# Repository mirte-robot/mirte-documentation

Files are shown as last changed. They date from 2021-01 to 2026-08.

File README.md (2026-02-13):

# Documentation MIRTE Robot

To build the documentation (requirement: Python3.10):

```sh
git clone https://github.com/mirte-robot/mirte-documentation
cd mirte-documentation
mkdir -p _modules/mirte-python
git clone https://github.com/mirte-robot/mirte-python _modules/mirte-python
python3 -m venv docs-env
source docs-env/bin/activate
pip install -r requirements.txt
cd _modules/mirte-python
pip install .
cd ../../

make html
# OR
sphinx-multiversion . _build/html
```

## Host locally
```
sphinx-reload . --watch doc/ _static/ _modules/  # browser will open automatically, don't forget the dot.
```
## Test

The documentation must pass the following two checks. Warnings are allowed, errors not.
```sh
make html && make linkcheck
```

## Spelling
Check for spelling with the following command
```sh
make spelling
```
Add correct words to the ```spelling_wordlist.txt``` file.

## Multi version setup
As the docs build uses other parts (ROS, Python, ...), just using sphinx-multiversion doesn't work 100%.
New setup:
- At release of a new version, a site.zip is created with the docs of that version without any other versions or version selector
- At creation of a new pages:
  - create dummy tags to generate the correct versions html
  - sphinx-multiversions build
  - for each release:
    - download the site.zip from the release page
    - take the versions html code from the 'dummy' and replace it in the downloaded version
  - push to github pages

How to create new version:
- change conf.py to new tag
- change _static/index.html to point to latest version.
- add new main version to build.yml:6: the releases env variable.

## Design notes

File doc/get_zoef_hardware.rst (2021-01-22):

Get the Zoef Hardware
#####################

Currently it is only possible to order all the parts yourself. In the futuer we will make it easier to buy a full Zoef Basic Box with all the listed components. 

Since we really want the robot to be upgradable, we will also support at least the mentioned alternatives/upgrades. At the moment the *italic* items are not yet supported though.

.. |check| raw:: html

    <input checked=""  type="checkbox">

+---------------------------+--------------------------------------------------+-------------------------------------------+
|                           | Zoef Basic                                       | Alternatives/Upgrades                     |
+===========================+==================================================+======================+====================+
| Computer                  | Orange Pi Zero (set 2 [1]_)                      | *Raspberry Pi 2/3/4* | *Jetson Nano 2GB*  |
+---------------------------+--------------------------------------------------+----------------------+--------------------+
| SD card                   | *TBD*                                            | Any 8Gb+ SD card                          |
+---------------------------+--------------------------------------------------+-----------------+-------------------------+
| Microcontroller           | STM32                                            | Arduino Nano    | *ESP8266*               |
+---------------------------+--------------------------------------------------+-----------------+-------------------------+
| Electrical circuit        | Zoef PCB                                         | Breadboard [3]_ | Powered breadboard [4]_ |
+---------------------------+--------------------------------------------------+-----------------+-------------------------+
| 3 pin cable               | 4x JST                                           | 4 x female-female dupont                  |
+---------------------------+--------------------------------------------------+-------------------------------------------+
| 4 pin cable               | 4x JST                                           | 4 x female-female dupont                  |
+---------------------------+--------------------------------------------------+-------------------------------------------+
| Micro USB cable 90 deg    |                                                  |                                           |
+---------------------------+--------------------------------------------------+ dupont cable                              |
| Micro USB cable short     |                                                  |                                           |
+---------------------------+--------------------------------------------------+-------------------------------------------+
| Battery                   | 5000mAh power bank [2]_                          | *12V battery pack with step down*         | 
+---------------------------+--------------------------------------------------+-------------------------------------------+
| Chassis                   | Zoef diff drive wood                             | *Zoef diff drive 3D print*                |
+---------------------------+--------------------------------------------------+-------------------------------------------+
| Nuts and bolts            | 15x M3                                           | *M3 with standoffs*                       |
+---------------------------+--------------------------------------------------+-------------------------------------------+
| Ball caster               | W420                                             |                                           |                 
+---------------------------+--------------------------------------------------+-------------------------------------------+
| Wheels                    | 2x Yellow TT motor wheel                         |                                           |
+---------------------------+--------------------------------------------------+-------------------------------------------+
| Motors                    | 2x TT motor male dupont                          | *TBD*                                     |
+---------------------------+--------------------------------------------------+-----------------+-------------------------+
| Motor driver              | L9110s                                           | L298N [5]_      | MX1919                  |
+---------------------------+--------------------------------------------------+-----------------+-------------------------+
| **Optional**                                                                                                             |
+---------------------------+--------------------------------------------------+-------------------------------------------+
| Wheel encoders            | 2x HC-020K                                       | *TBD*                                     |
+---------------------------+--------------------------------------------------+-------------------------------------------+
| Distance sensors          | 2x HC-SR04                                       |                                           |
+---------------------------+--------------------------------------------------+-------------------------------------------+
| Line follow sensors       | 2x TCRT5000                                      | *TBD*                                     |
+---------------------------+--------------------------------------------------+-------------------------------------------+
| Keypad                    | 5 button keypad                                  |                                           |
+---------------------------+--------------------------------------------------+-------------------------------------------+
| USB Camera                | HM1355                                           |                                           |
+---------------------------+--------------------------------------------------+-------------------------------------------+
| Displays                  | 2x 128x64 OLED                                   |                                           |
+---------------------------+--------------------------------------------------+-------------------------------------------+
| Servo                     | SG90                                             |                                           |
+---------------------------+--------------------------------------------------+-------------------------------------------+

.. [1] The extension board is optional, but needed when using the USB camera.
.. [2] This power bank will fit the wooden frame. Any powerbank with a stable 5V will work.
.. [3] With a breadboard, the JST and USB cables need to be replacd by dupont cables.
.. [4] With a powered breadboard the JST cables need to be replaced by dupont cables.
.. [5] Due to teh voltage drop this will not work well with a 5V powerbank.

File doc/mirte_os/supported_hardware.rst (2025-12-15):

.. _supported-hardware:

Supported Hardware
##################

Microcontroller Peripherals
***************************

Raw pins
========

.. tabs::

   .. group-tab:: ROS

      .. code-block:: bash

         $ ros2 service call /io/get_analog_pin_value mirte_msgs/srv/GetAnalogPinValue "{pin: }"
         $ ros2 service call /io/get_digital_pin_value mirte_msgs/srv/GetDigitalPinValue "{pin: }"
         $ ros2 service call /io/set_digital_pin_value mirte_msgs/srv/SetDigitalPinValue "{pin: ,value: false}"
         $ ros2 service call /io/set_pwm_pin_value mirte_msgs/srv/SetPWMPinValue "{pin: ,value: false}"

      Setting a pin can be either 'analog' (PWM) or 'digital'. The pin itself can be defined
      as the print on the MCU (e.g. 'GP3'). You can have a look in the web interface to
      see all options. 

   .. group-tab:: Python

      .. code-block:: python
      
         from mirte_robot import robot
         mirte = robot.createRobot()

         mirte.getAnalogPinValue()

      .. automethod:: robot.Robot.setAnalogPinValue
         :noindex:

      .. automethod:: robot.Robot.getAnalogPinValue
         :noindex:

      .. automethod:: robot.Robot.setDigitalPinValue
         :noindex:

      .. automethod:: robot.Robot.getDigitalPinValue
         :noindex:

   .. group-tab:: Blockly

      

.. warning::
    Currently there is no check on whether a pin is already in use by some hardware defined
    in the yaml configuration discussed earlier. Therefore there is no expected behavior 
    when using getting or setting raw pins.

DC Motor
========

Depending on the interface of your motor controller, the DC motor can be controlled though three
different interfaces:

   - **ddp** (digital, digital, pwm): This interface uses two digital pins to set the direction of
     the motor, and uses a PWM dignal to set the speed. The L298 can use this interface.
   - **dp** (digital, pwm): This interface uses one digital pin for teh direction, and pwm for the speed.
     The downside is that the motor will slightly 'kick' when switching between forward and backward.
     This can be done on both L298 and L9110.
   - **pp** (pwm, pwm): This interface uses two PWM signals to control the motor. The downside is that
     this will take up 2 PWM pins. Can be used on both L298 and L9110.

As you can see the choice for interface depends on the actual interface provided by the motor
controller, and the number of (PWM) pins you have available on the MCU.

ddp (e.g. L298)
---------------
.. code-block:: yaml

   motor:
     left:
       name: left
       device: mirte
       type: ddp
       pins:
         d1: GP19
         d2: GP18
         p1: GP17     # pwm

dp (e.g. L298 or L9110)
-----------------------

.. code-block:: yaml

   motor:
     left:
       name: left
       device: mirte
       type: dp
       pins:
         d1: GP19
         p1: GP18      # pwm

pp (e.g. L298 or L9110)
-----------------------

.. code-block:: yaml

   motor:
     left:
       name: left
       device: mirte
       type: pp
       pins:
         p1: GP19       # pwm
         p2: GP18       # pwm

.. tabs::

   .. group-tab:: ROS

      .. code-block:: bash

         $ ros2 service call /io/motor/left/set_speed mirte_msgs/srv/SetMotorSpeed "{speed: 50}"

   .. group-tab:: Python

      .. code-block:: python
      
         from mirte_robot import robot
         mirte = robot.createRobot()

         mirte.setMotorSpeed('left', 50)

      .. automethod:: robot.Robot.setMotorSpeed        
         :noindex:

   .. group-tab:: Blockly

      

The motors will be defined separately. In this case there are two motors called 'left_motor' and 
'right_motor', both controlled on the 'mirte' device defined above. The pins are set corresponding 
to the L9110s motor driver.

.. warning::
   
   Please not that it is adviced to call the motors 'left' and 'right'. You can chose your own names
   when you are only using these interfaces. In order to also get the ROS twist message (and steering
   in the web interface to work) you **need** to have the motors called 'left' and 'right'.

Servo
=====
.. code-block:: yaml

   servo:
     left:
       name: left
       device: mirte
       pins:
         pin: GP3

.. tabs::

   .. group-tab:: ROS

      .. code-block:: bash

         $ ros2 service call /io/servo/right/set_angle mirte_msgs/srv/SetServoAngle "{angle: 90, degrees: true}"

   .. group-tab:: Python

      .. code-block:: python
      
         from mirte_robot import robot
         mirte = robot.createRobot()

         mirte.setServoAngle('left', 90)

      .. automethod:: robot.Robot.setServoAngle        
         :noindex:

   .. group-tab:: Blockly

      

Keypad
======
.. code-block:: yaml

   encoder:
     left:
       name: left
       device: mirte
       pins:
         pin: GP28     # analog input

.. tabs::

   .. group-tab:: ROS

      As a topic (non-blocking):

      .. code-block:: bash

         $ ros2 topic echo /io/keypad/left

      As a service (blocking):

      .. code-block:: bash

         $ /io/keypad/left/get_key

   .. group-tab:: Python

      .. code-block:: python
      
         from mirte_robot import robot
         mirte = robot.createRobot()

         mirte.getKeypad('left')

      .. automethod:: robot.Robot.getKeypad        
         :noindex:

   .. group-tab:: Blockly

      

OLED
====
.. code-block:: yaml

   oled:
     left:
       name: left
       device: mirte
       pins:
         scl: GP5
         sda: GP4

.. tabs::
   
   .. group-tab:: ROS

      .. code-block:: bash

         $ ros2 service call /io/oled/right/set_text mirte_msgs/srv/SetOLEDText "{text: 'hello'}"

   .. group-tab:: Python

      .. code-block:: python
      
         from mirte_robot import robot
         mirte = robot.createRobot()

         mirte.setOLEDText('left', 'hello mirte')

      .. automethod:: robot.Robot.setOLEDText        
         :noindex:

   .. group-tab:: Blockly

      

Distance sensor
===============
.. code-block:: yaml

   distance:
     left:
       name: left
       device: mirte
       pins:
         trigger: GP7
         echo: GP6

.. tabs::
   
   .. group-tab:: ROS

      As a topic (non-blocking):

      .. code-block:: bash

         $ ros2 topic echo /io/distance/left/get_range

      As a service (blocking):

      .. code-block:: bash

         $ ros2 service call /io/distance/left/get_range mirte_msgs/srv/GetRange

   .. group-tab:: Python

      .. code-block:: python
      
         from mirte_robot import robot
         mirte = robot.createRobot()

         mirte.getDistance('left')

      .. automethod:: robot.Robot.getDistance
         :noindex:

   .. group-tab:: Blockly

      

IR sensor
=========
.. code-block:: yaml

   intensity:
     left:
       name: left
       device: mirte
       pins:
         digital: GP16
         analog: GP26     # analog input

.. tabs::
   
   .. group-tab:: ROS

      As a topic (non-blocking):

      .. code-block:: bash

         $ ros2 topic echo /io/intensity/left
         $ ros2 topic echo /io/intensity/left/digital

      As a service (blocking):

      .. code-block:: bash

         $ ros2 service call /io/intensity/left/get_analog mirte_msgs/srv/GetIntensity
         $ ros2 service call /io/intensity/left/get_digital mirte_msgs/srv/GetIntensityDigital

   .. group-tab:: Python

      .. code-block:: python
      
         from mirte_robot import robot
         mirte = robot.createRobot()

         mirte.getIntensity('left')

      .. automethod:: robot.Robot.getIntensity
         :noindex:

   .. group-tab:: Blockly

      

Color sensor
============
.. code-block:: yaml

   color:
     left:
       name: left
       device: mirte
       pins:
       pins:
         scl: GP5
         sda: GP4

.. tabs::

   .. group-tab:: ROS

      As a topic (non-blocking):

      .. code-block:: bash

         $ ros2 topic echo /io/color/left/hsl
         $ ros2 topic echo /io/color/left/rgb

      As a service (blocking):

      .. code-block:: bash

         $ ros2 service call /io/intensity/left/get_analog mirte_msgs/srv/GetIntensity
         $ ros2 service call /io/intensity/left/get_digital mirte_msgs/srv/GetIntensityDigital

   .. group-tab:: Python

      .. code-block:: python

         from mirte_robot import robot
         mirte = robot.createRobot()

         mirte.getColor('left')['h']

      .. automethod:: robot.Robot.getColor
         :noindex:

   .. group-tab:: Blockly

      

USB Camera
**********

By default the robot assumes you have connected the supported USB cam.
Currently only a ROS interface is defined.

.. tabs::

   .. group-tab:: ROS

      The camera image is published in three ways (using `ROS image transport <http://wiki.ros.org/image_transport>`_).

      .. code-block:: bash

         $ rostopic echo /webcam/image_raw
         $ rostopic echo /webcam/image_raw/compressed
         $ rostopic echo /webcam/image_raw/theora

Other USB Cameras
=================

In case you have another USB webcam, you might need to change the parameters of the `USB cam <https://wiki.ros.org/usb_cam>`_ to
reflect your webcam. This then needs to be changed in the `launchfile <https://github.com/mirte-robot/mirte-ros-packages/blob/3cbfac4a66425defc56f39b94bafca7794dd227e/mirte_bringup/launch/minimal.launch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>`_:

.. code-block:: bash      

   $ v4l2-ctl --list-formats-ext
   $ nano /home/mirte/mirte_ws/src/mirte_bringup/launch/minimal.launch

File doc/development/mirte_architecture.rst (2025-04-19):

Software Architecture Overview
##############################

.. warning::
   Currently none of the interfaces (hardware, software) are definitive. This means that we might still
   change this. Developing educational material around MIRTE is possible, but you should be able to
   modify this in case we change the interfaces.

Software Architecture
=====================

As the robot is meant for education, most of the design decisions we made were made with that in mind. This
means we were forced to make decisions in the speed vs usability (/learnability) tradeoff and decided to go
for the learnability over speed. We this improving speed should, at some point, be done by the students
themselves.

.. tabs::

   .. tab:: Overall

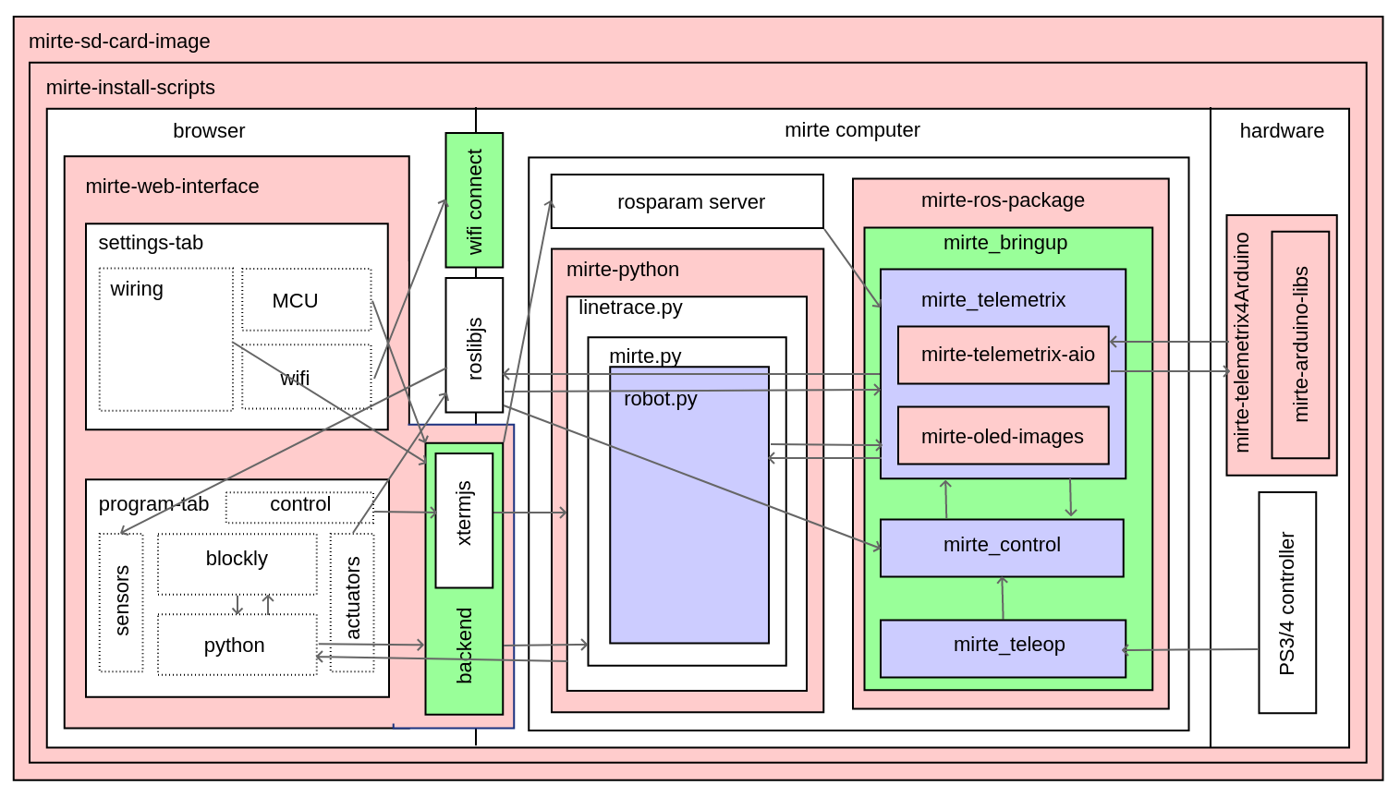
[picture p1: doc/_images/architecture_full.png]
Full Software Architecture
      

      Full architecture overview of the MIRTE software. Repositories are shown in red, ROS nodes in blue, and
      systemd services in green. More explanation can be found in the corresponding tabs. The dataflow is
      shown with arrows and will be explained in the next section.

   .. tab:: Repositories

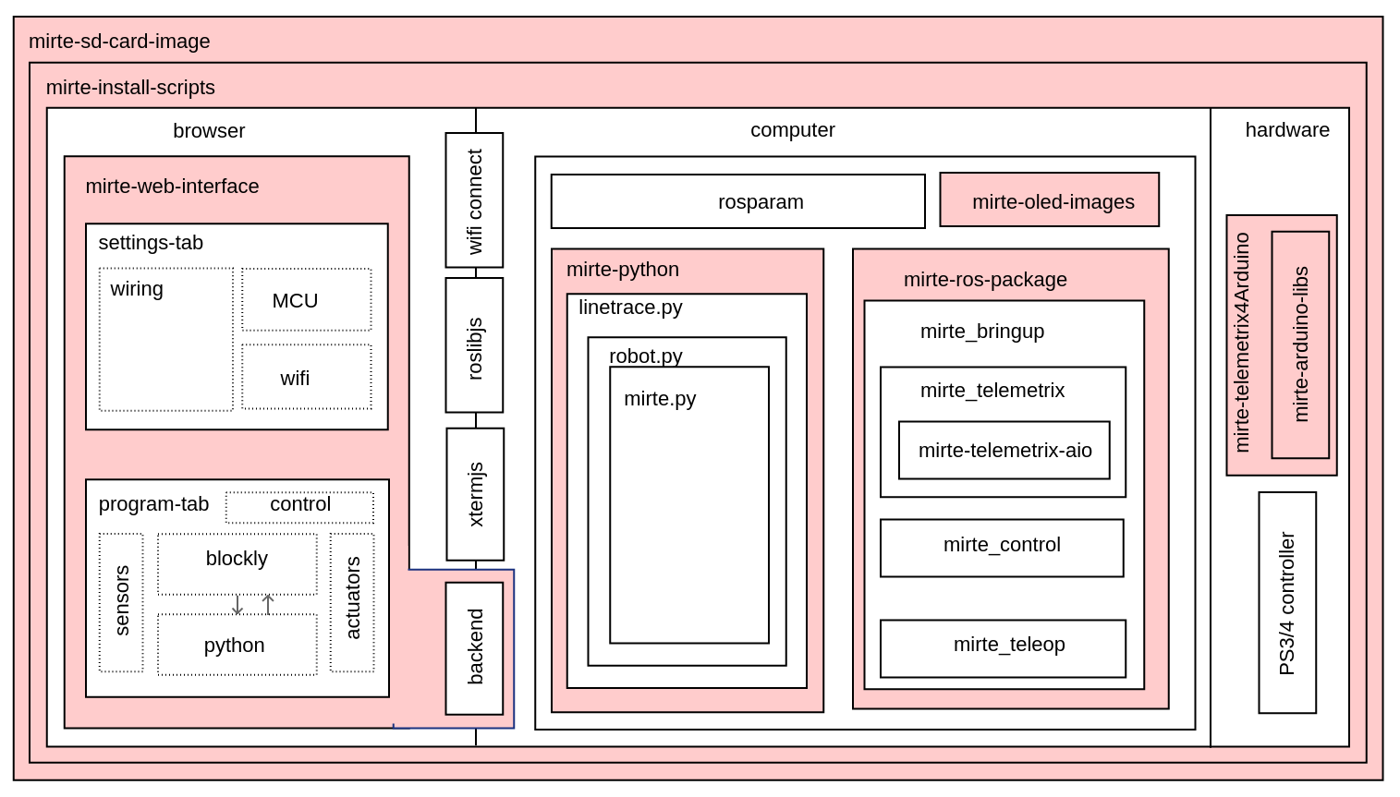
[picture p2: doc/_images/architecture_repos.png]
Overview of software repositories.
      

      The software of MIRTE is stored in multiple repositories on `github <https://github.com/mirte-robot>`_, 
      but can also be found on the MIRTE robot in /usr/local/src/mirte. 
 
      - `mirte-web-interface <https://github.com/mirte-robot/mirte-web-interface>`_: Is the repository 
        where the Vue frontend and nodeJS backend are stored. They are in one repository since they are 
        frequently updated together.
      - `mirte-python <https://github.com/mirte-robot/mirte-python>`_: Contains the python API of the
        sensors and actuators. This basically is a wrapper around the ROS topics and services for all
        the sensors and actuators.
      - `mirte-ros-packages <https://github.com/mirte-robot/mirte-ros-packages>`_: Contains the ROS packages
        to communicate with the hardware (MCU, PS controller, camera, etc) and the differential drive controller.
      - `mirte-telemetrix-aio <https://github.com/mirte-robot/telemetrix-aio>`_: Is a fork of
        telemetrix-aio to also support our own wheel encoder library (needed to get the interrupts of the encoder).
      - `mirte-telemetrix4Arduino <https://github.com/mirte-robot/Telemetrix4Arduino>`_: Is a fork 
        of telemetrix4Arduino to also add support for the wheel encoder.
      - `mirte-arduino-libraries <https://github.com/mirte-robot/mirte-arduino-libraries>`_: Contains the
        implementation of our own wheel encoder.
      - `mirte-oled-images <https://github.com/mirte-robot/mirte-oled-images>`_: Contains the images and
        image sequences to show on the OLED.
      - `mirte-install-scripts <https://github.com/mirte-robot/mirte-install-scripts>`_: Contains all scripts
        needed to install the MIRTE software on the robot. This includes our own repositories and dependencies,
        but also creates a user and enables the Wifi AP and systemd services.
      - `mirte-sd-image-tools <https://github.com/mirte-robot/mirte-sd-image-tools>`_: Contains all things 
        needed to build an ARM sd card image with everything installed from the mirte-install-scripts repo 
        for both the Orange Pi Zero 2 (Armbian Ubuntu) and Raspberry Pi (Ubuntu). 

   .. tab:: ROS nodes

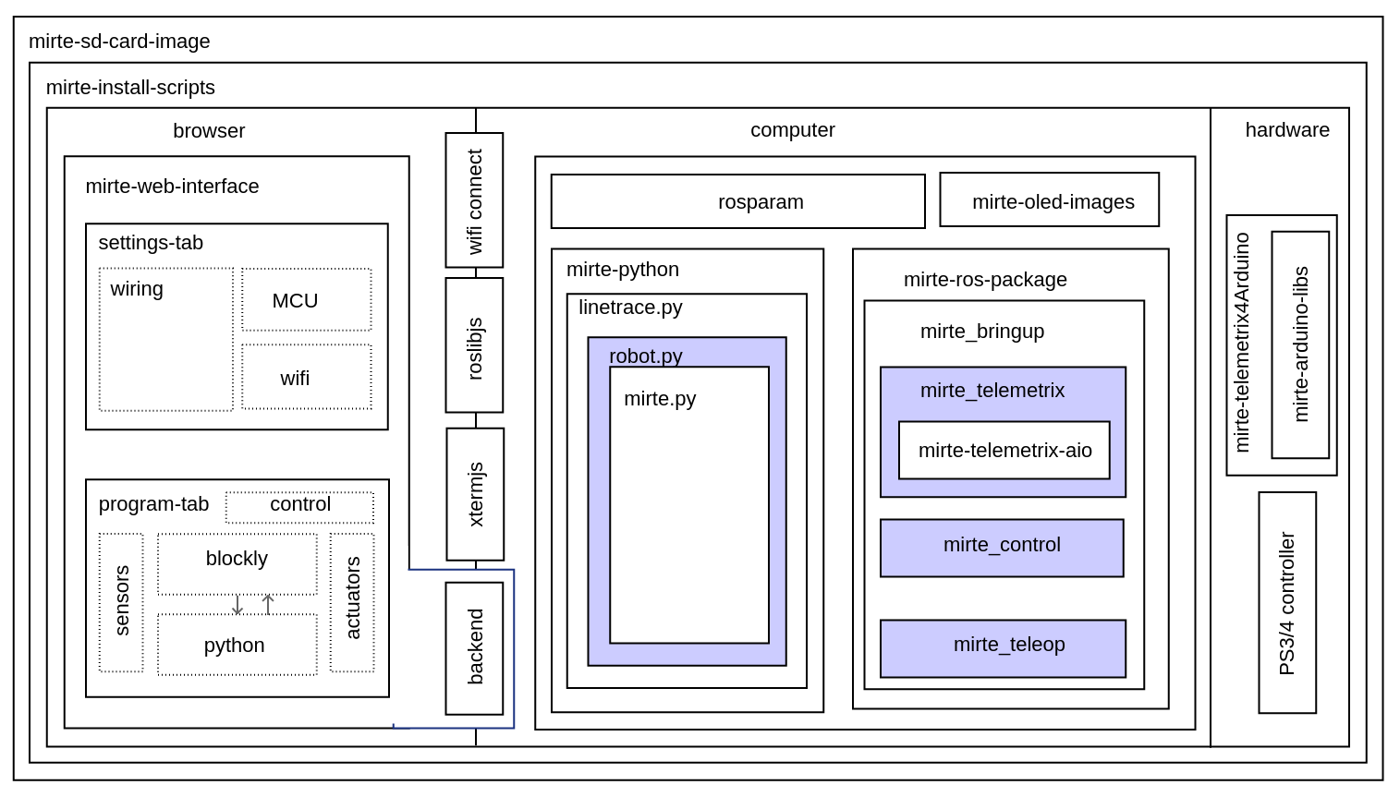
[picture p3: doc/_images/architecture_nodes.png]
Overview of ROS nodes.
      

      A couple of ROS nodes are used to control the robot (please note that the default for ROS packages
      are underscores):

      - **mirte_telemetrix**: This node initializes the telemetrix-aio pins based on the settings in the ROS
        parameter server. Each actuator will create a corresponding service. Each sensor will create
        both a service and a topic.
      - **mirte_control**: This is the ROS control wrapper for a differential drive robot. ROS control
        will already account for the kinematics from Twist message to rad/s per wheel. This rad/s per
        wheel is then transformed to speed (range -100 to 100) of the robot. 
      - **mirte_teleop**: This can be the teleop-key or teleop-joy node. In both cases the input from the
        device will be transformed into a Twist message.
      - **robot.py**: The robot.py node is included in the user defined python script. When run, this will
        start as a node as well. This node is only active when the user runs their script.

   .. tab:: Systemd

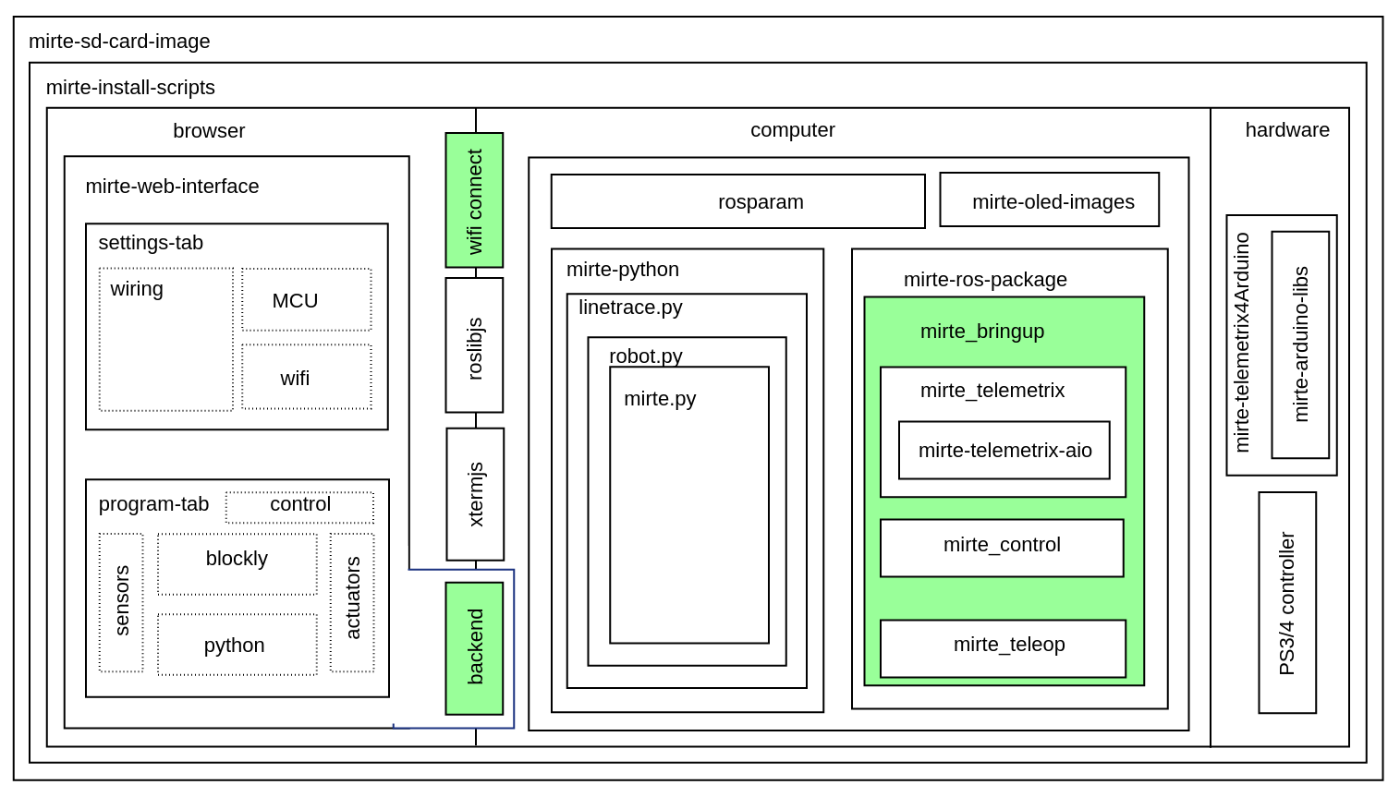
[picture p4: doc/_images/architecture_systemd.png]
Systemd services.
      

      In order to start all needed software on boot there are 3 systemd services activated:

      - **mirte-ap**: Service which starts the wifi-connect software. This will bring up a Wifi AP when
        no connection to a known network can be established. Otherwise it will connect to the known
        router. This service is executed as root.
      - **mirte-web-interface**: Service starts the web interface backend. The backend will also serve
        the frontend built by VueJS. This service is executed as the mirte user.
      - **mirte-ros**: Service will bringup ROS by launching minimal.launch.  This service is executed 
        as the mirte user.
      - **mirte-jupyter**: Service will start Jupyter Notebook which can be accessed on port 8888.

      All of them will start at boot, but can also be stopped:

      .. code-block:: bash

         mirte$ sudo service mirte-ros stop

      , started:

      .. code-block:: bash

         mirte$ sudo service mirte-ros start

      , or inspected:

      .. code-block:: bash

         mirte$ sudo journalctl -u mirte-ros -f

Software Flows
==============

.. tabs::

   .. tab:: Settings

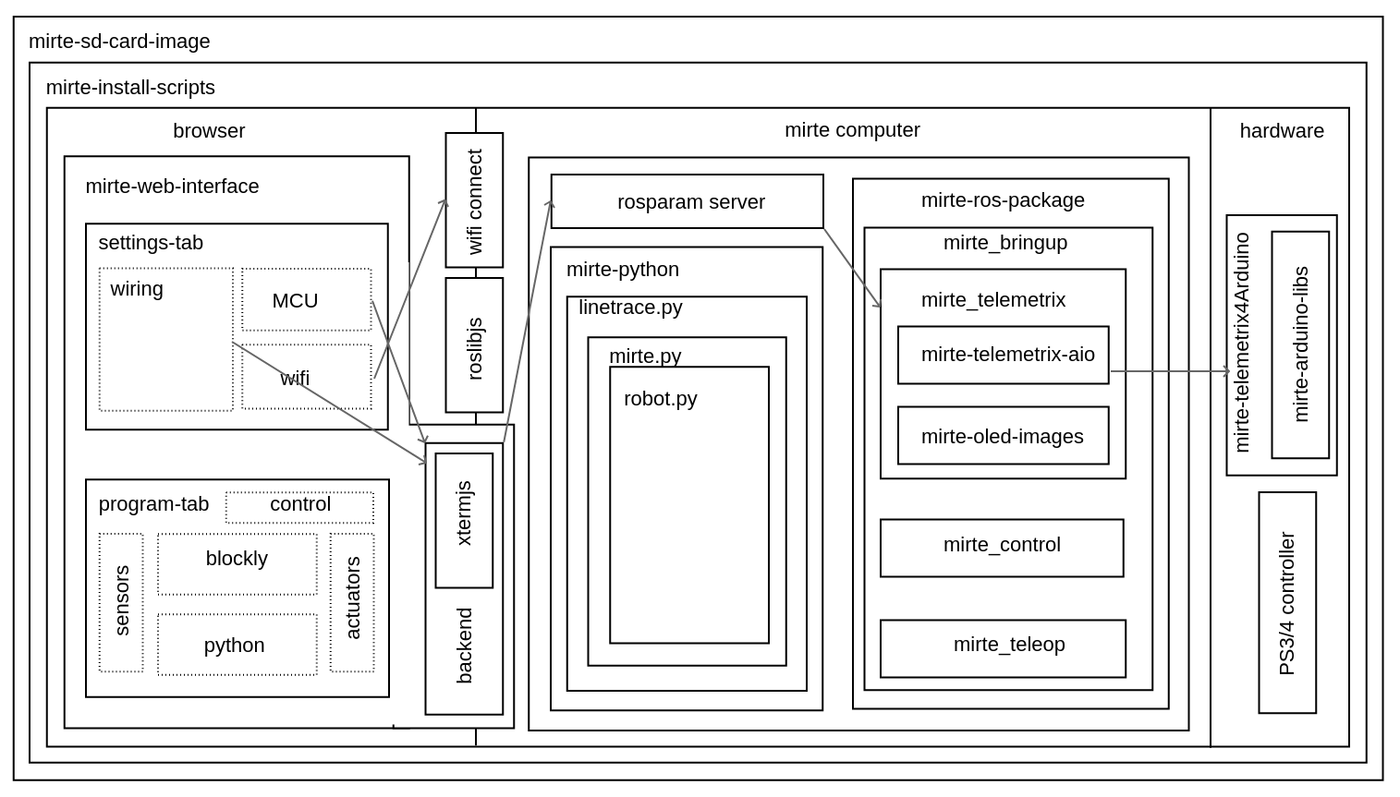
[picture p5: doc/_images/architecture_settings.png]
Settings flow.
      

      Like described earlier there are some things that you need to set before you can use the
      robot. This involves both uploading telemetrix to the MCU, and defining the connected
      hardware. Both can be done via commandline and web interface.

      When uploading telemetrix to the MCU from the web interface, a request will be sent to 
      the backend to execute the same command as you would execute when in a terminal.

      When a user changes the settings in the web interface a YAML file is generated and uploaded 
      via the backend to the robot. This will overwrite the mirte_user_config.yaml file and 
      overwrite the parameters in the running parameter server. The backend will also stop the 
      running telemetrix node and restart it so the initialization will be done again with the new 
      parameters. By restarting the telemetrix node, this node will get the new settings from
      the parameter server and initialize this using mirte-telemetrix-aio which will apply it
      on the MCU with mirte-telemetrix4Arduino.

      You can also connect to your own wifi. Whe doing this from the web interface, it will
      communicate the change right away to the wifi-connect server which will use NetworkManager
      accordingly.

      .. note::

         In the current implementation the YAML config is generated in the web interface
         and uploaded to the robot through the backend. We will redesign this in the future
         and implement a version where the web interface will communicate via roslibjs and
         therefore also be able to reflect the settings as they are.

      .. note::

         Usually one does not change the parameters within a running ROS system. We do think
         that these kind of settings belong to the parameter server since they usually do not
         change. In this educational robot we try to also make it easy to modify your robot.

   .. tab:: Sensors

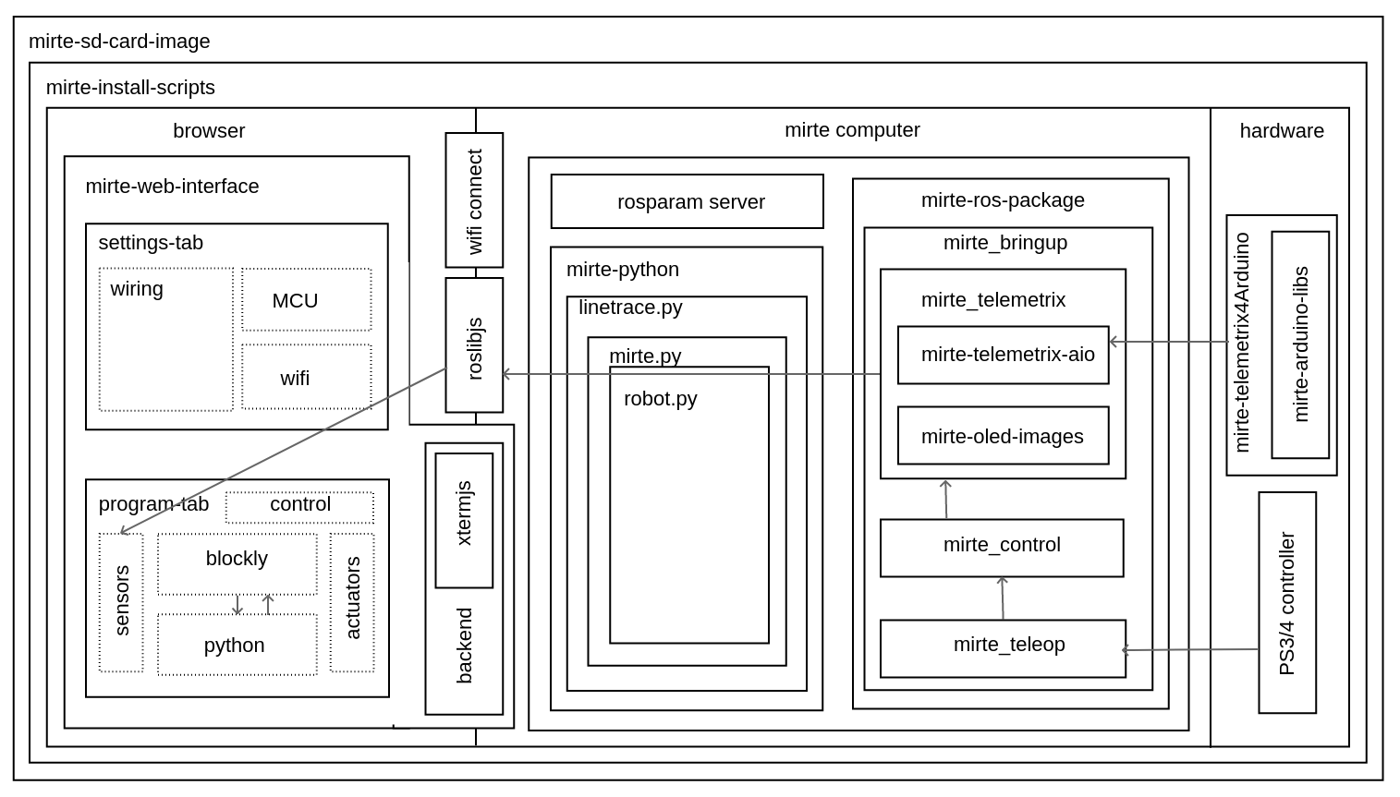
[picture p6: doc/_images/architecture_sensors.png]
Sensor data flow.
      

      Sensordata are read continuously in telemetrix (with a preset frequency). They are then
      communicated over USB from the MCU via mirte-telemetrix4Arduino to mirte-telemetrix-aio.
      The ROS node ROS_telemetrix_api.py from mirte_telemetrix will read these values as they
      get in via the callback from mirte-telemetrix-aio. They will then be published as a topic,
      and the last value is stored in order to be returned by a service call. These sensor
      values will the be send to the webinterface via roslibjs.

   .. tab:: Actuators

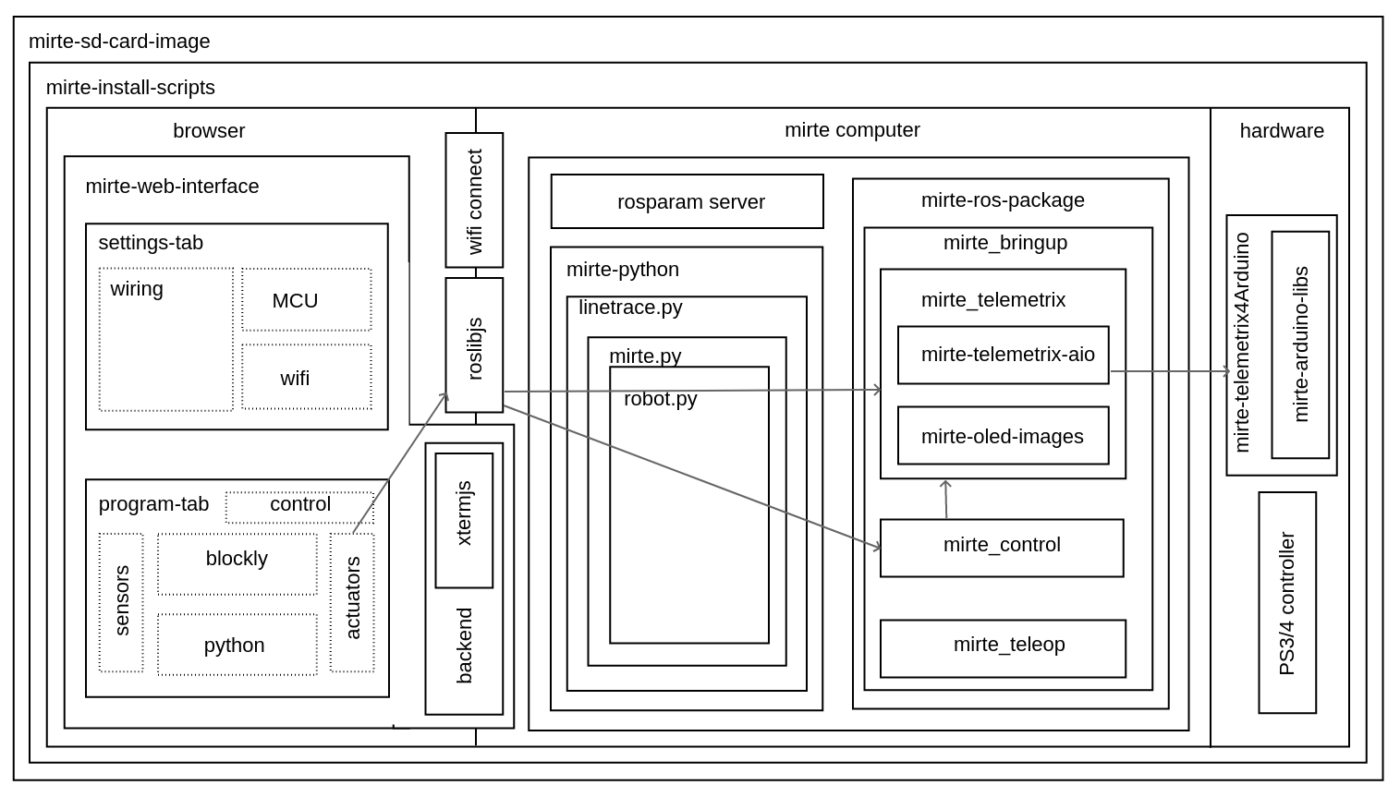
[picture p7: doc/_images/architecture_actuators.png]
Actuator data flow.
      

      When a user changes the actuator values in the web interface this will be communicated to
      the ROS_telemetrix_api.py node from mirte-telemetrix-aio (or to mirte-control in case 
      a Twist message is generated to drive around). The ROS_telemetrix_api.py node will the
      call the corresponding mirte-telemetrix-aio function which will pass this to 
      mirte-telemetrix4Arduino on the MCU.

   .. tab:: Python

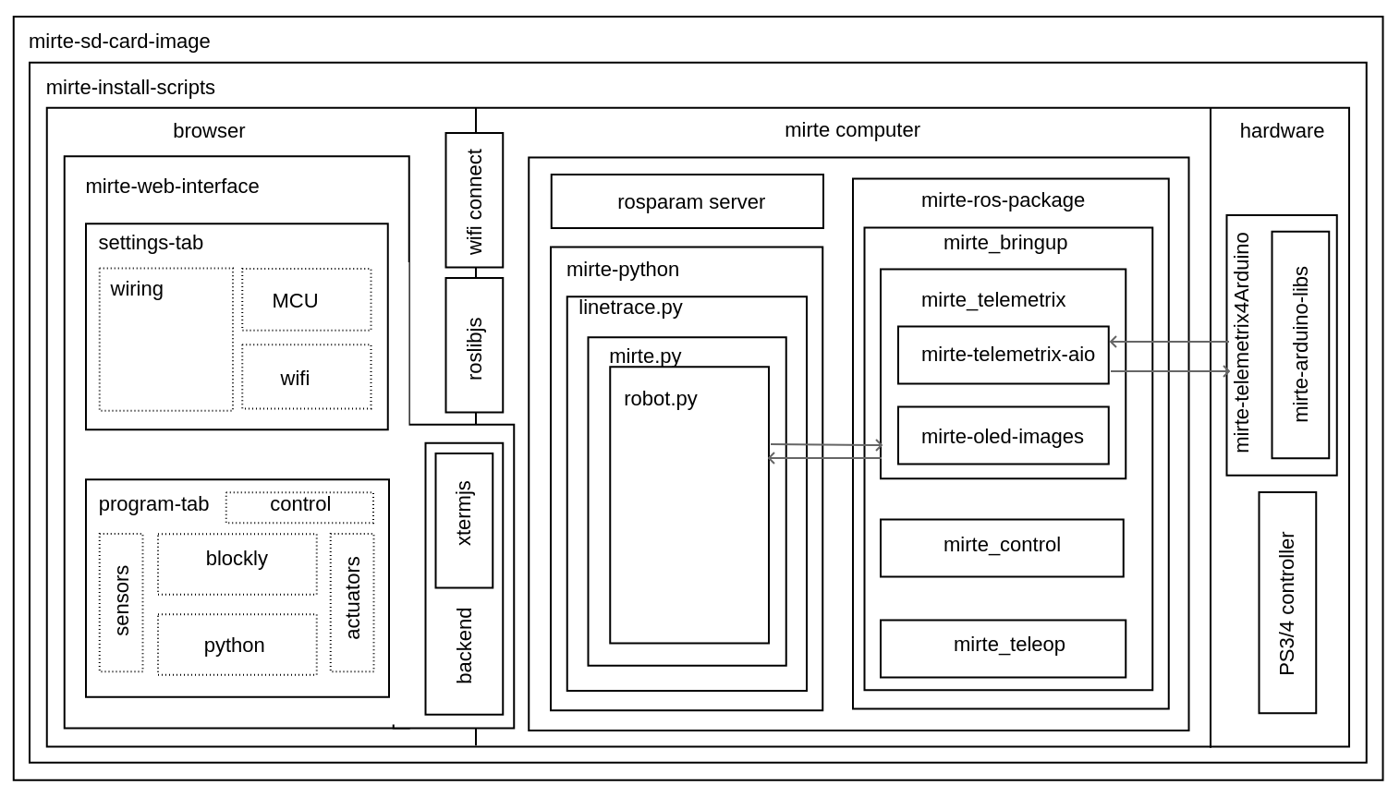
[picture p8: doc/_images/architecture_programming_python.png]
Python programming flow.
      

      TODO

   .. tab:: Blockly

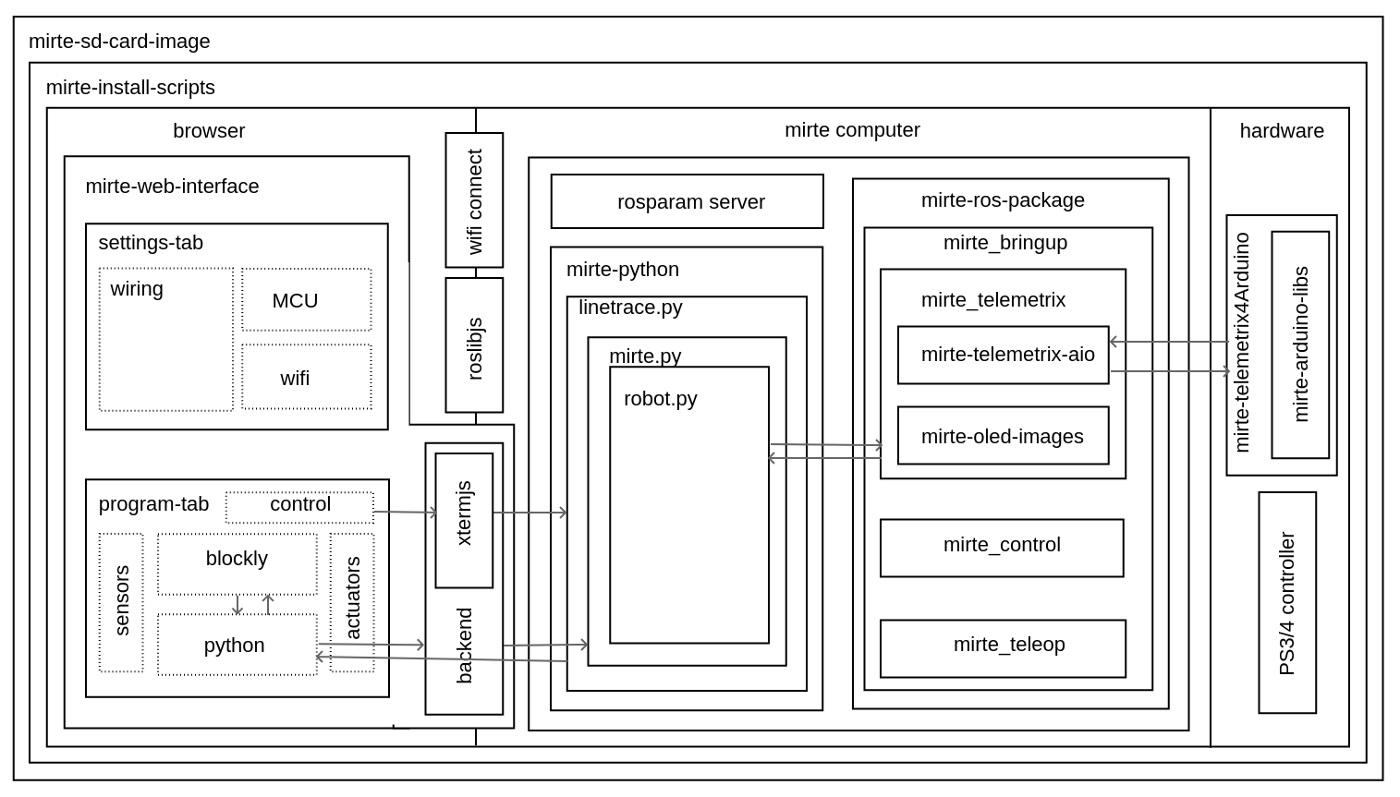
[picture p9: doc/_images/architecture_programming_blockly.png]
Blockly programming flow.
      

      TODO

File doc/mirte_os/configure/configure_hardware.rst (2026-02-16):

Specify Hardware
================

This step in only needed in case you are not using the MIRTE PCB (or followed the 
breadboard instructions). For other MCUs (or other wiring of the Raspberry Pi Pico) the software still
needs to know which pin is connected to what kind of hardware. This can be done in two ways.

From the Web Interface
----------------------

On the webinterface this can be done by removing and adding the peripherals in order
to match your robot hardware:

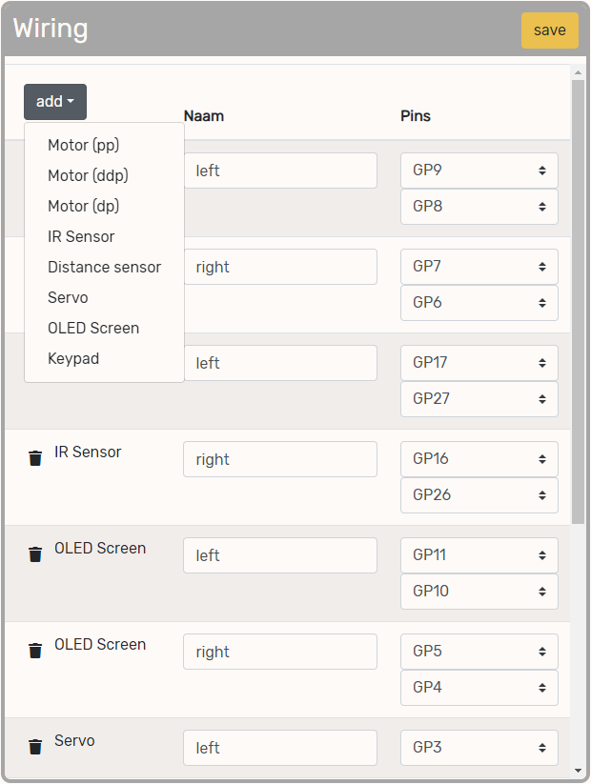
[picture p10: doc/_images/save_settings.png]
Save settings
      

From the Terminal
-----------------

The configuration to map the pins to sensortypes is done in `/usr/local/src/mirte/mirte-ros-packages/mirte_bringup/telemetrix_config/mirte_user_config.yaml <https://github.com/mirte-robot/mirte-ros-packages/blob/main/mirte_bringup/telemetrix_config/mirte_user_config.yaml>`_. 
This file consists of multiple sections needed for MIRTE to know which pins to control. 
The default settings are the MIRTE PCB. Below we will got though all sections (of the 
Raspberry Pi Pico on a breadboard).

.. code-block:: yaml

   device:
     mirte:
       type: breadboard
       board: pico                     # [pico, blackpill_f103c8, nanoatmega328]
       max_frequency: 50

Each config needs to state which type of device is is controlling. In this case we have 
one device called 'mirte' of type 'breadboard' with a 'pico' on it. The sampling frequency
is set to 50Hz, so every 2ms new sensor data will come in. Please note that your 
max_frequency might depend on the number of sensors you have connected. The more sensors
you connect, the lower the sampling frequency can get. If your sampling frequency is too
high you will notice a delay in the data.

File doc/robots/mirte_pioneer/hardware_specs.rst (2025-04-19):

Hardware specs
##############

One of the goals of MIRTE is to be modular and extendable. Therefore MIRTE has a minimal amount
of custom designed components, and mostly uses frequently used hardware. Two exceptions are
the `base <https://github.com/mirte-robot/mirte-frame>`_ (which can be lasercut, 3D printed, or 
any existing base you already have) and the `PCB <https://github.com/mirte-robot/mirte-pcb>`_ 
(which is optional and can be replaced by a breadboard as well). 

Below you will find the components that are used in the MIRTE Pioneer kit, which gives you a basic
mobile platform, and can be extended with optional sensors and actuators. Or you could use
alternatives/upgrades for certain parts.

Currently it is only possible to order all the parts yourself. In the future we will make it easier
to buy a full MIRTE Pioneer Box with all the listed components.

.. list-table::
   :widths: 25 25 50
   :header-rows: 1

   * - 
     - MIRTE Pioneer
     - Alternatives/Upgrades
   * - Computer
     - `Orange Pi Zero 2 <http://www.orangepi.org/html/hardWare/computerAndMicrocontrollers/details/Orange-Pi-Zero-2.html>`_
     - Raspberry Pi 3/4, Orange Pi 3B
   * - micro SD card
     - Intenso 16Gb (class 10) micro SD card
     - Any 16Gb+ micro SD card 
   * - Microcontroller
     - Raspberry Pi Pico H (RP2040)
     - Arduino Nano/Uno | SMT32 
   * - Electrical circuit
     - `MIRTE PCB <https://github.com/mirte-robot/mirte-pcb>`_
     - Breadboard [#f1]_ + `MB102 <https://www.aliexpress.com/item/1005001863057390.html>`_ + `splitter <https://www.aliexpress.com/item/4001025724405.html>`_
   * - 3 pin cable
     - 4x JST XH
     - 4x female-female dupont
   * - 4 pin cable
     - 4x JST XH
     - 4x female-female dupont
   * - Micro USB cable short
     - 1x
     - Dupont Cables
   * - Battery
     - `Intenso XS10000 <https://www.intenso.de/en/products/powerbanks/xs5000-xs10000-xs20000>`_
     - Any stable powerbank [#f2]_
   * - Chassis
     - `MIRTE diff drive wood <https://github.com/mirte-robot/mirte-frame>`_
     - MIRTE diff drive 3D print
   * - Nuts and bolts
     - 15x M3 15mm
     -
   * - Ball caster
     - `W420 (thin shape) <https://www.aliexpress.com/item/32734869856.html>`_
     -
   * - Wheels
     - `2x Yellow TT motor wheel <https://www.aliexpress.com/item/4000122298687.html>`_
     -
   * - Motors
     - `2x TT motor male dupont <https://www.aliexpress.com/item/32918824820.html>`_
     -
   * - Motor driver
     - `L9110s <https://www.aliexpress.com/item/32679413836.html>`_
     - `L298N <https://www.aliexpress.com/1005001621936295.html>`_ [#f3]_,  `MX1919 <https://www.aliexpress.com/item/32954393390.html>`_
   * - **Optional**
     -
     -
   * - Distance sensors
     - `2x HC-SR04 <https://www.aliexpress.com/item/4000232170787.html>`_
     -
   * - Line follow sensors
     - `2x TCRT5000 <https://www.aliexpress.com/item/32968870340.html>`_
     -
   * - Keypad
     - `5 button keypad <https://www.aliexpress.com/item/2044851328.html>`_
     -
   * - Displays
     - `2x 128x64 I2C OLED <https://www.aliexpress.com/item/1005001621806398.html>`_
     -
   * - Servo
     - `SG90 <https://www.aliexpress.com/item/1005001621918352.html>`_
     - Any servo supported by Arduino
   * - USB Camera
     - `OV9726 <https://www.aliexpress.com/item/1005005093538299.html>`_
     - Any USB camera

.. rubric:: Footnotes

.. [#f1] With a breadboard, the JST and USB cables need to be replaced by dupont cables.
.. [#f2] This power bank will fit the wooden frame. Any powerbank with a stable 5V will work.
.. [#f3] Due to the voltage drop of the L298N this will not work nicely with a 5V powerbank.

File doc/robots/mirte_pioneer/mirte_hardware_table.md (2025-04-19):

:orphan:

| | MIRTE Pioneer | Alternatives/Upgrades |
| --- | --- | --- |
| Computer | [Orange Pi Zero 2](http://www.orangepi.org/html/hardWare/computerAndMicrocontrollers/details/Orange-Pi-Zero-2.html) | | 
| SD card | Intenso 8Gb | Any 8Gb+ SD card | 
| Microcontroller | Raspberry Pi Pico (RP2040) | Arduino Nano/Uno or SMT32
| Electrical | [MIRTE PCB](https://github.com/mirte-robot/mirte-pcb) | Breadboard [^1] + circuit [MB102](https://www.aliexpress.com/item/1005001863057390.html) + [splitter](https://www.aliexpress.com/item/4001025724405.html) | 
| 3 pin cable | 4x JST XH | 4 x female-female dupont | 
| 4 pin cable | 4x JST XH | 4 x female-female dupont | 
| Micro USB cable short | 1x | Dupont Cables | 
 | Battery | [Intenso XS10000](https://www.intenso.de/en/products/powerbanks/xs5000-xs10000-xs20000/) | Any stable powerbank [^2] | 
 | Chassis | [MIRTE diff drive wood](https://github.com/mirte-robot/mirte-frame) | MIRTE diff drive 3D print | 
 | Nuts and bolts | 15x M3 | | 
 | Ball caster | [W420 (thin shape)](https://www.aliexpress.com/item/32734869856.html) | | 
 | Wheels | [2x Yellow TT motor wheel](https://www.aliexpress.com/item/4000122298687.html) | | 
 | Motors | [2x TT motor male dupont](https://www.aliexpress.com/item/32918824820.html) | | 
 | Motor driver | [L9110s](https://www.aliexpress.com/item/32679413836.html) | [L298N](https://www.aliexpress.com/item/1005001621936295.html) [^3] or [MX1919](https://www.aliexpress.com/item/32954393390.html) | 
 | **Optional** | | 
 | Distance sensors | [2x HC-SR04](https://www.aliexpress.com/item/4000232170787.html) | | 
 | Line follow sensors | [2x TCRT5000](https://www.aliexpress.com/item/32968870340.html) | | 
 | Keypad | [5 button keypad](https://www.aliexpress.com/item/2044851328.html) | | 
 | Displays | [2x 128x64 I2C OLED](https://www.aliexpress.com/item/1005001621806398.html) | | 
 | Servo | [SG90](https://www.aliexpress.com/item/1005001621918352.html) | Any servo supported by Arduino | 
 | USB Camera | [OV9726](https://www.aliexpress.com/item/1005005093538299.html) | Any USB camera | 
----------------------

**Footnotes**

[^1]: With a breadboard, the JST and USB cables need to be replaced by dupont cables.

[^2]: This power bank will fit the wooden frame. Any powerbank with a stable 5V will work.

[^3]: Due to the voltage drop of the L298N this will not work nicely with a 5V powerbank.

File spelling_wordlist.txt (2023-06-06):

Mirte
mirte
Arduino
arduino
Linux
linux
Blockly
blockly
mDNS
bluetooth
bluetoothctl
passwd
Telemetrix
telemetrix
Nano
Uno
launchfile
platformio
wifi
ini
systemd
bringup
api
cpp
scp
Jupyter
ROS
microcontroller
IP
hostname
Teleop
cmd
vel
PWM

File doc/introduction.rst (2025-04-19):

MIRTE (MIRTE, an Inspiring Robot for Technology Education) is yet another robot developed for
education. Robotics, due to the its multidisciplinary nature, is a good way to teach about STEM
eduction. This is why a lot of robotics kits have been developed already. So why yet another?
We believe that robotic kits for education should be cheap, open source, not only focus on the
software, have as few custom parts as possible, and should be useful from primary/elementary school
all the way to university. Getting you to the next level in each discipline step by step.

+-------------+--------------------------------------------------------------------------------------------------------------------------------+
| Software    | from `Blockly <https://developers.google.com/blockly>`_ to `Python <https://www.python.org/>`_ to `ROS <https://www.ros.org>`_ |
+-------------+--------------------------------------------------------------------------------------------------------------------------------+
| Electrical  | from custom PCB with Raspberry Pi Pico (RP2040), to breadboard with STM32/Arduino                                              |
+-------------+--------------------------------------------------------------------------------------------------------------------------------+
| Mechanical  | from wooden frame to own made (3D printed) frames                                                                              |
+-------------+--------------------------------------------------------------------------------------------------------------------------------+
| Interaction | from cute to purely functional                                                                                                 |
+-------------+--------------------------------------------------------------------------------------------------------------------------------+

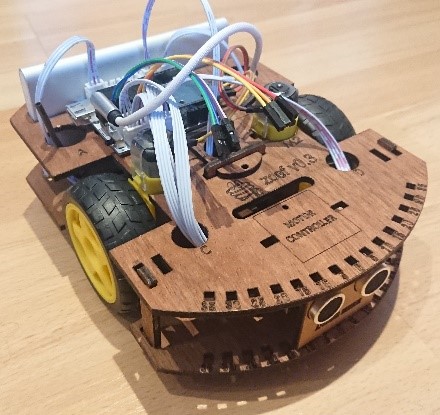
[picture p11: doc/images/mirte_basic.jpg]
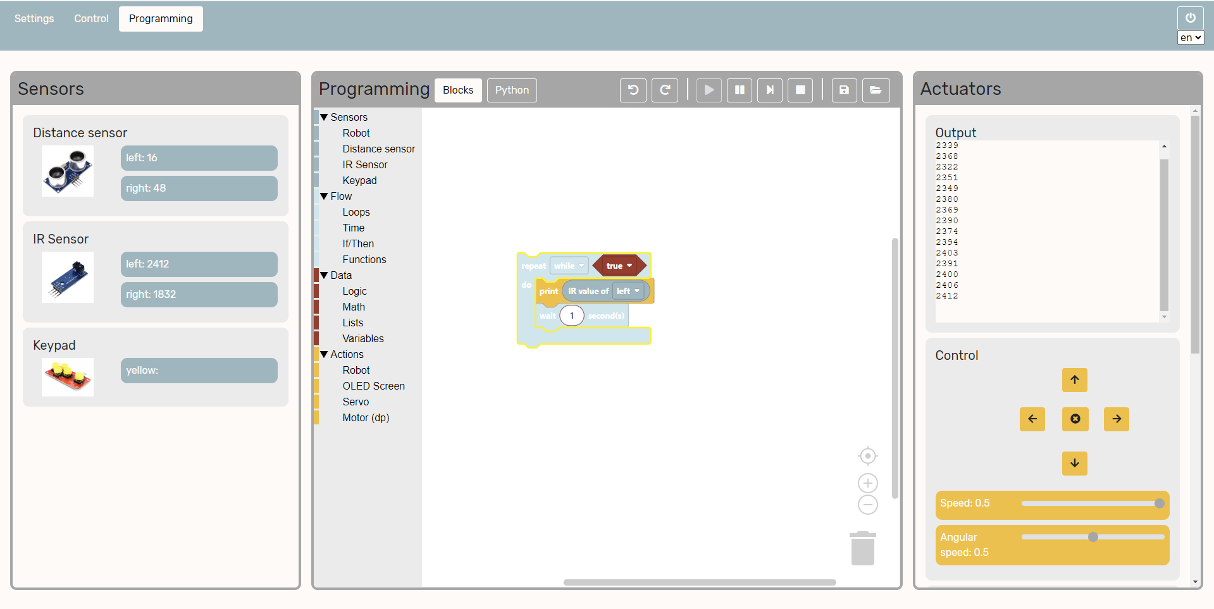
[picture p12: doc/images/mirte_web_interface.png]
.. ..  

.. 

..

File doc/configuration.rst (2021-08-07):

Configure Software to match Hardware
####################################

This step in only needed in case you are not using the Mirte PCB (or followed the STM breadboard instructions). For other MCUs teh software still needs to know which pin is connected to what kind of hardware. This can be done in two ways.

From the Web Interface
=======================

From the Terminal
=======================

The configuration to map the pins to sensorstypes is done in /usr/local/src/mirte/mirte_control/config/mirte_base_config.yaml. This file consists of multiple sections needed for Mirte to know which pins to control. For convenience there are already three examples given for the STM32 on a breadboard, the Mirte PCB and an Arduino nano on a breadboard. The default settings are the Mirte PCB. Below we will got though all sections (of the STM32 on a breadboard).

Device
------
.. code-block:: yaml

   device:
     mirte:
       type: breadboard               # [breadboard, mirte_pcb], mirte_pcb implies a stm32 as mcu
       mcu: stm32                     # [stm32, nano, nano_old]
       samping_interval: 10           # integer in ms

Each config needs to state which type of device is is controlling. In this case we have one device called 'mirte' of type 'breadboard' with a 'stm32' on it. The sampling interval is set to 10ms (100Hz), being the interval the data will be communicated from the mcu. 

Motor
-----
.. code-block:: yaml

   motor:
     left_motor:
       device: mirte
       pins:
         1a: D5               # pin needs PWM
         1b: D6               # pin needs PWM
     right_motor:
       device: mirte
       pins:
         1a: D9               # pin needs PWM
         1b: D10              # pin needs PWM

The motors will be defined seperately. In this case there are two motors called 'left_motor' and 'right_motor', both controlled on the 'mirte' device defined above. The pins are set corrsponding to the L9110s motor driver. Other motor drivers will also work but the 1a/b refernce does not make sense.

Wheel encoder
-------------
.. code-block:: yaml

   encoder:
     left_encoder:
       device: mirte
       pins:
         pin: D2            # pin needs interrupt support
       ticks_per_wheel: 20
     right_encoder:
       device: mirte
       pins:
         pin: D3            # pin needs interrupt support
       ticks_per_wheel: 20

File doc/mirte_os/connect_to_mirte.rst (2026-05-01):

.. _connect:

Connect to MIRTE
################

When the MIRTE robot boots up she will check if she can connect to a known Wifi network (i.e. a 
network which the robot has connected to before). If this fails, she will start her own 
access point (AP) to which you can connect. 

There are multiple ways to connect to your MIRTE robot. The availability depends on the SBC 
(Orange Pi Zero 2 or Raspberry Pi 2/3/4) you use. This section describes these options.

.. note::
   
   When connecting though wireless AP, or USB, you will be connected to the robot through ethernet. 
   You will therefore not have access to internet on your machine. 

Wireless Access Point
=====================

After booting up MIRTE for the first time the robot is in access point (AP) mode and a wifi network 
will be available with ssid Mirte-XXXXXX (where each X is hex 1-F). You can connect to this network 
with the password 'mirte_mirte'. While in AP mode, the ip address of MIRTE is 192.168.42.1, but you 
could also access it with mirte.local or mirte-XXXXXX.local:

.. code-block:: bash
   
   $ ping mirte.local

.. code-block:: bash
   
   $ ping mirte-XXXXXX.local

.. code-block:: bash
   
   $ ping 192.168.42.1

In a classroom setting there might me multiple MIRTE APs available. It is advised to prepare the
robots in advance and write down the ssid per robot. If this is not possible one could also
get the unique XXXXXX value by analyzing the red and green LED on the Orange Pi Zero 2 (this is not 
yet supported for the Raspberry Pi). 

Count the number of blinks of the red LED until the green one blinks. This is one of the X's in
the ssid. Please note that this is hexadecimal, so 10 will be A, 11 will be B etc). Do this until 
you have all 6 X's. Please note that the start of the sequence (and thus the start of the first X) 
is shown by blinking both red and green. The full XXXXXX will be communicated in this way for 5 
times.

Wireless Client Mode
====================

The downside of having MIRTE in AP mode, is that both your computer and the MIRTE robot do not
have access to the internet. By connecting the MIRTE robot to another access point (e.g. router)
you can still use the internet while controlling your robot.

If you are not in control of your own router, you can also create one youself by putting your mobile 
phone in hotspot mode, or put your computer (on Windows) in mobile hotspot mode.

You can connect MIRTE to your local wifi network from either of the two interfaces (web or
terminal). You therefore first need to connect to MIRTE in AP mode and following the instructions 
from the :ref:`next section<Accessing the interface>`. 

.. note::
   Since the MIRTE robot is probably still in AP mode when you try to do this, you will only see 
   the Wifi networks that were visible when the robot booted. It is therefore adviced to first 
   start a hostpot/router/AP and then (re)boot the MIRTE robot.

.. note::
   Currently the MIRTE robot is not able to connect to WPA3 networks.

.. warning::
   Before connecting to another Access Point, make sure you have set a new password on the
   MIRTE robot. This can be done in any terminal (ssh or vscode):

   .. code-block:: bash

      mirte$ passwd

   Otherwise you will not be able to login to any web interface (mirte web, or vscode), and
   need to set the password via ssh.

From terminal
-------------

The most stable way to connect the MIRTE robot to another network will be to login to the MIRTE
robot via ssh, manually setting the network settings. The following command will ask for the 
SSID and password of the AP to connect to and reboot:

.. code-block:: bash

   mirte$ read -p "SSID: " ssid && read -p "Password: " -s password && nmcli connection add con-name Mirte-connection type wifi ifname wlan0 wifi.ssid $ssid wifi-sec.key-mgmt wpa-psk wifi-sec.psk $password && sudo reboot now

You can also try a less stable version, where the robot will not reboot but will try to
connect right away. This command will sleep for 10 seconds and then try to connect to your wifi. 
The 10 seconds sleep is done to make sure the AP connection will be disconnected properly.

.. code-block:: bash

   mirte$ nohup `$(sleep 10; sudo nmcli d wifi connect <wifi_SSID> password <wifi_password>)` & sudo nmcli d disconnect wlan0

.. note::
   This will freeze your terminal since the ssh connection was disconnected since the
   wifi changed. You can get your terminal back typing '~.' (tilde point).

From web interface
------------------

In the web interface there is also an option to connect to your local wifi. In your favorite
browser visit http://mirte.local/#/Settings and select the network and password. This will also
try to connect to the wifi right away and might therefore be less successfull.

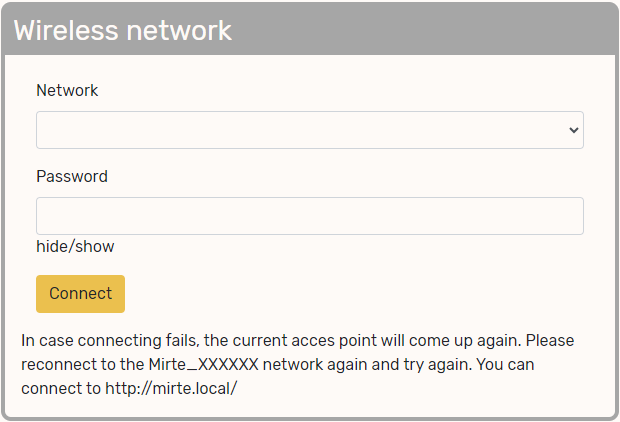
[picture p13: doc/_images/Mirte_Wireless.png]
Alternative text


.. warning::

   Only access points that were online when MIRTE booted will be listed.

Other (wired) options
=====================

USB connection
--------------

When connecting to Wifi is not possible you can also connect through USB. In this case you need
to connect the power of the Orange Pi Zero 2 via USB with your computer. After booting up a wired
network will be available with which you can connect. While in USB mode, the ip address of MIRTE
is 192.168.43.1, but you could also access it with mirte.local or mirte-XXXXXX.local:

.. code-block:: bash
   
   $ ping mirte.local

.. code-block:: bash
   
   $ ping mirte-XXXXXX.local

.. code-block:: bash
   
   $ ping 192.168.43.1

Wired Ethernet
--------------

You can also connect a wired ethernet cable using MIRTE. Make sure you connect an ethernet cable
to a router with DHCP enabled so your robot will get an ip address from the router:

.. code-block:: bash
   
   $ ping <ip-address from router>

There are multiple ways to get the ip address from the router. On Linux and MacOS the easiest
way is to ping for mirte.local:

.. code-block:: bash
   
   $ ping mirte.local

.. note::

   mDNS is not supported by Windows and therefore you can not use mirte.local in this setup.

   When possible you could also log into your router and see what ip address the router assigned.
   If this also is not an option you could also decode the ip address from the blinking scheme 
   (as described above in the Wireless section). This currently is only supported for the Orange Pi
   Zero 2.

.. note::
  
   You can also connect the wired cable when already connected to Wireless. This will enable
   internet (through your router) to the robot, but not to your own computer.

TTL debug
---------

If all of this fails, you can still debug your MIRTE robot through the TTL interface. The easiest
way to do this is by using a TTL-USB device and connect to the MIRTE. If you have no clue what
this means, you will probably not use this. If you do understand, you can search the internet
to see how to connect to your SBC.

Renaming MIRTE
==============

In some cases it might be useful to rename the unique ID of your MIRTE (the XXXXXX part). 
This can be done by changing the linux hostname:

.. code-block:: bash

   mirte$ sudo bash -c "echo Mirte-<new ID> > /etc/hostname"
   mirte$ sudo reboot now

You should now be able to connect to Mirte-<new ID>.

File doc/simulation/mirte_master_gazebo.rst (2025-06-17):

MIRTE Master
############

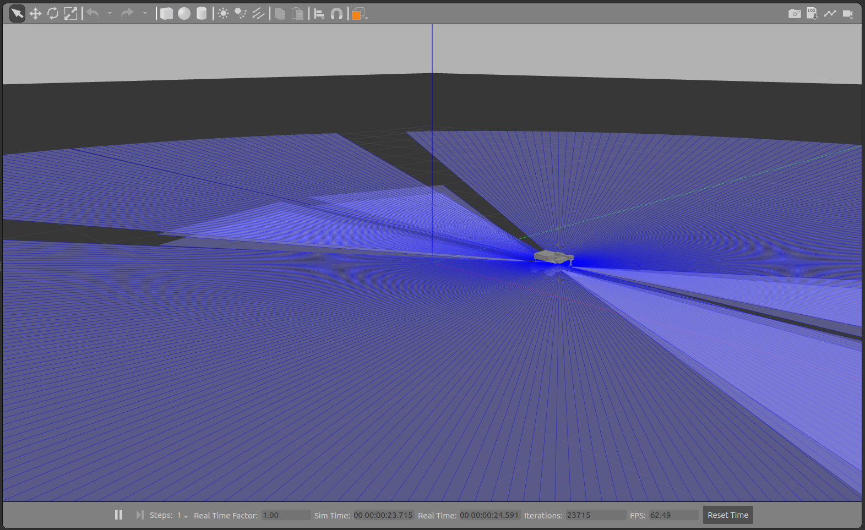
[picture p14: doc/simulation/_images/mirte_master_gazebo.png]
MIRTE Master in Gazebo Classic


To start the MIRTE Master in simulation you can:

.. code-block:: bash

   $ ros2 launch mirte_gazebo gazebo_mirte_master_empty.launch.xml

This will start the simulation, including all controllers. In this way
you can control the base, the arm and the gripper.

Controlling the base
--------------------

To control the base, you can send a Twist message to the same cmd_vel
topic as on the physical MIRTE robot (/mirte_base_controller/cmd_vel_unstamped).
The easiest way of doing so, is using the teleop_twist_keyboard package:

.. code-block:: bash

   $ ros2 run teleop_twist_keyboard teleop_twist_keyboard --ros-args --remap cmd_vel:=/mirte_base_controller/cmd_vel_unstamped

Controlling the arm
-------------------

To control the arm, you can send a JointTrajectory message to the topic
(/mirte_master_arm_controller/joint_trajectory). You can move the arm up:

.. code-block:: bash

   $ ros2 topic pub --once /mirte_master_arm_controller/joint_trajectory trajectory_msgs/msg/JointTrajectory "{joint_names: ['shoulder_pan_joint', 'shoulder_lift_joint', 'elbow_joint', 'wrist_joint'], points: [{positions: [0.0, 0.0, -1.56, 1.56], time_from_start:{ sec: 3, nanosec: 0}}]}"

And move the arm down again:

.. code-block:: bash

   $ ros2 topic pub --once /mirte_master_arm_controller/joint_trajectory trajectory_msgs/msg/JointTrajectory "{joint_names: ['shoulder_pan_joint', 'shoulder_lift_joint', 'elbow_joint', 'wrist_joint'], points: [{positions: [0.0, -1.56, -1.56, 1.56], time_from_start:{ sec: 3, nanosec: 0}}]}"

The controller also accepts an action on /mirte_master_arm_controller/follow_joint_trajectory,
but this is mostyl usefull for MoveIt!

Controlling the gripper
-----------------------

To control the gripper, you can send an action to /mirte_master_gripper_controller/gripper_cmd. You cna close the gripper:

.. code-block:: bash

   $ ros2 action send_goal /mirte_master_gripper_controller/gripper_cmd control_msgs/action/GripperCommand "{command: {position: 0.1}}"

And open the gripper:

.. code-block:: bash

   $ ros2 action send_goal /mirte_master_gripper_controller/gripper_cmd control_msgs/action/GripperCommand "{command: {position: -0.1}}"

Planning with MoveIt!
---------------------

With the above command you can move the arm, but there is no planning involved. Nor does
it take collisions into account. This is why it makes sense to use MoveIt! In a 
seperate terminal, you can start Rviz with the MoveIt! 

You can follow the instructions in :ref:`MoveIt!<MoveIt!>`, ans skip the installation
part. And make sure to start the launchfile with the `use_sim_time` argument:

.. code-block:: bash

   $ ros2 launch mirte_moveit_config mirte_moveit.launch.py use_sim_time:=True

.. note::

   Please note that, in the simulation, you will get errors about the _mimic joints
   not being found. This is a `known issue <https://github.com/ros-controls/gazebo_ros2_control/issues/173>`_ 
   in the Humble gazebo_ros2_control package, but does not affect the working of the
   simulation.

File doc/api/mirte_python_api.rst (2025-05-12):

Python API
==========

This documentation is automatically generated based on the `source file <https://github.com/mirte-robot/mirte-python/blob/main/mirte_robot/robot.py>`_.

.. warning::

   This API is still under development and might still change. Please
   take this into account when developing (course material). 

.. autoclass:: robot.Robot
   :members:
   :undoc-members:

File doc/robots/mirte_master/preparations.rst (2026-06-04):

Preparations
############

Before you can assemble the robot it makes sense to prepare some parts.

MIRTE PCB
---------

.. carousel::
   :show_controls:
   :show_fade:
   :show_buttons_on_top:
   :show_captions_below:

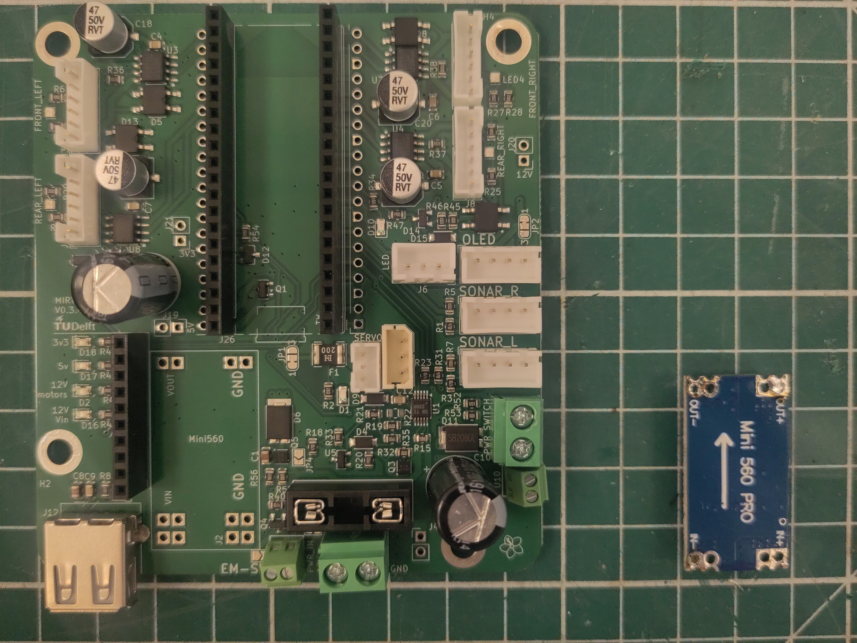
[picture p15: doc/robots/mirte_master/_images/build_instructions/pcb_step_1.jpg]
   
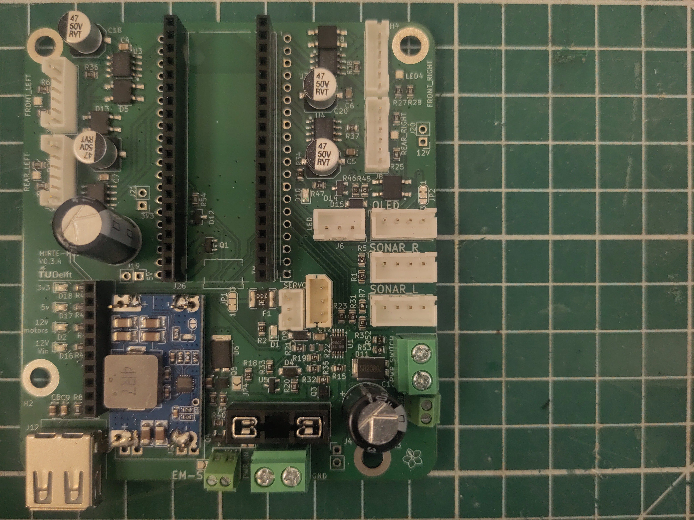
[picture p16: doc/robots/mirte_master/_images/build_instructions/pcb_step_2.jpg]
   

       ..

       Solder the step-down onto the PCB. Make sure to have it in the
       right direction.

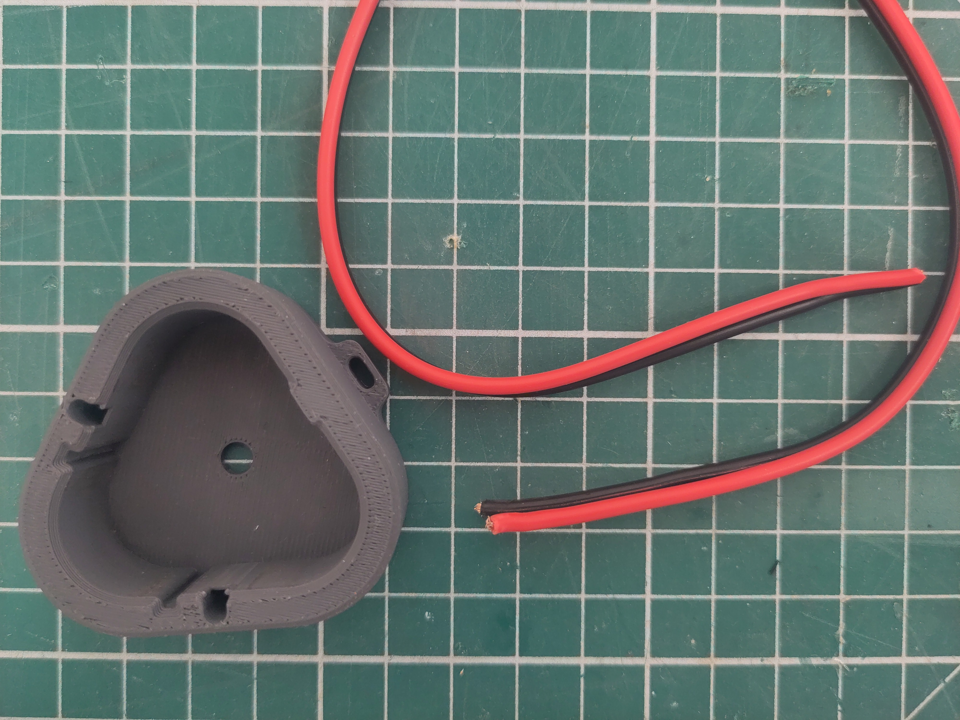
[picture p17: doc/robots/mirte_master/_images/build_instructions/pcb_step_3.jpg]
   
   
       ..

       Cut 30 cm of cable.

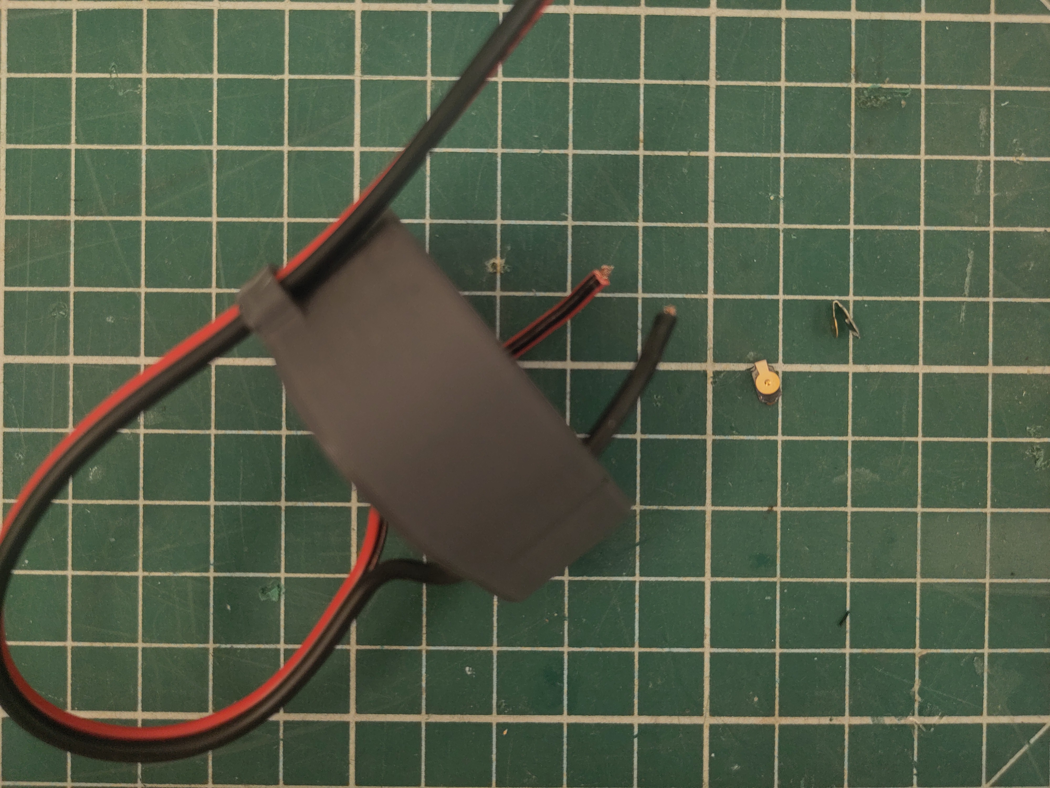
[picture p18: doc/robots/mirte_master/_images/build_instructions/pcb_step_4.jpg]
   

       ..

       Put the cable through the holes. Make sure the colors are on the
       correct side.

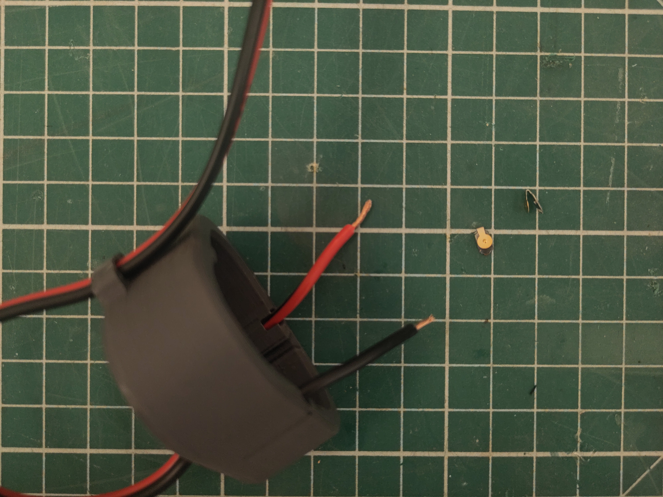
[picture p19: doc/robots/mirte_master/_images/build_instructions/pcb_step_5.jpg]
   

       ..

       Strip the ends.

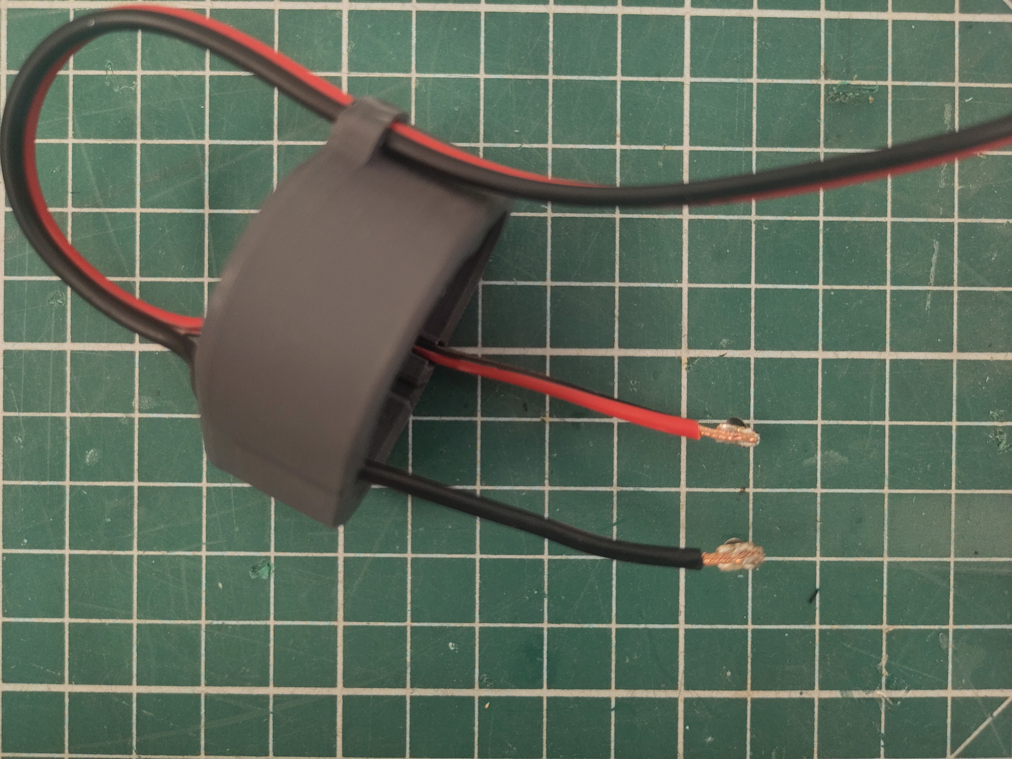
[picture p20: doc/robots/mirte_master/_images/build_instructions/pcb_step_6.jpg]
   

       ..

       And solder the spring contacts.

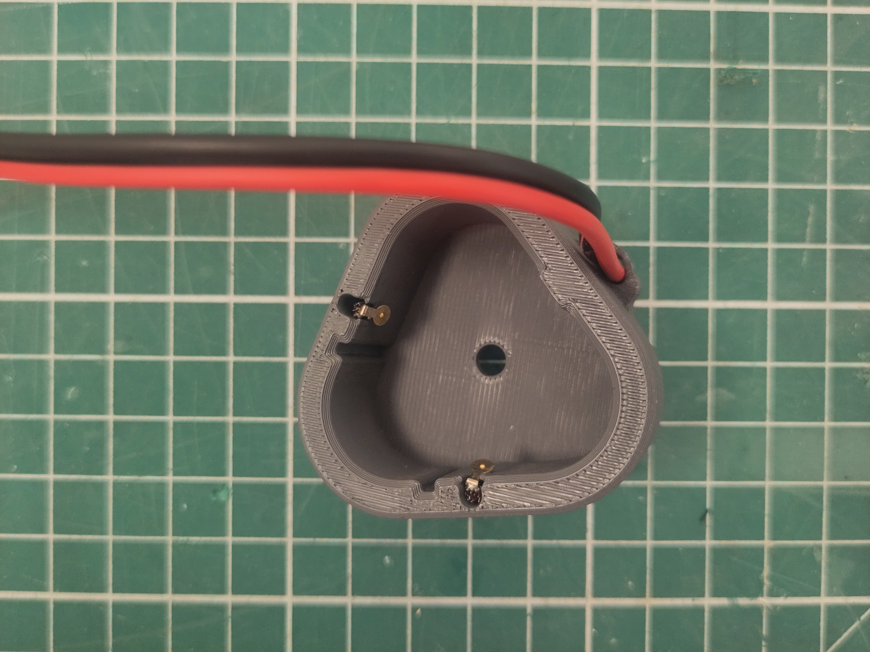
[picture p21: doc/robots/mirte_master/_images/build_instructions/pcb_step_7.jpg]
   

       ..

       Put the spring contacts in place and tighten the cable.

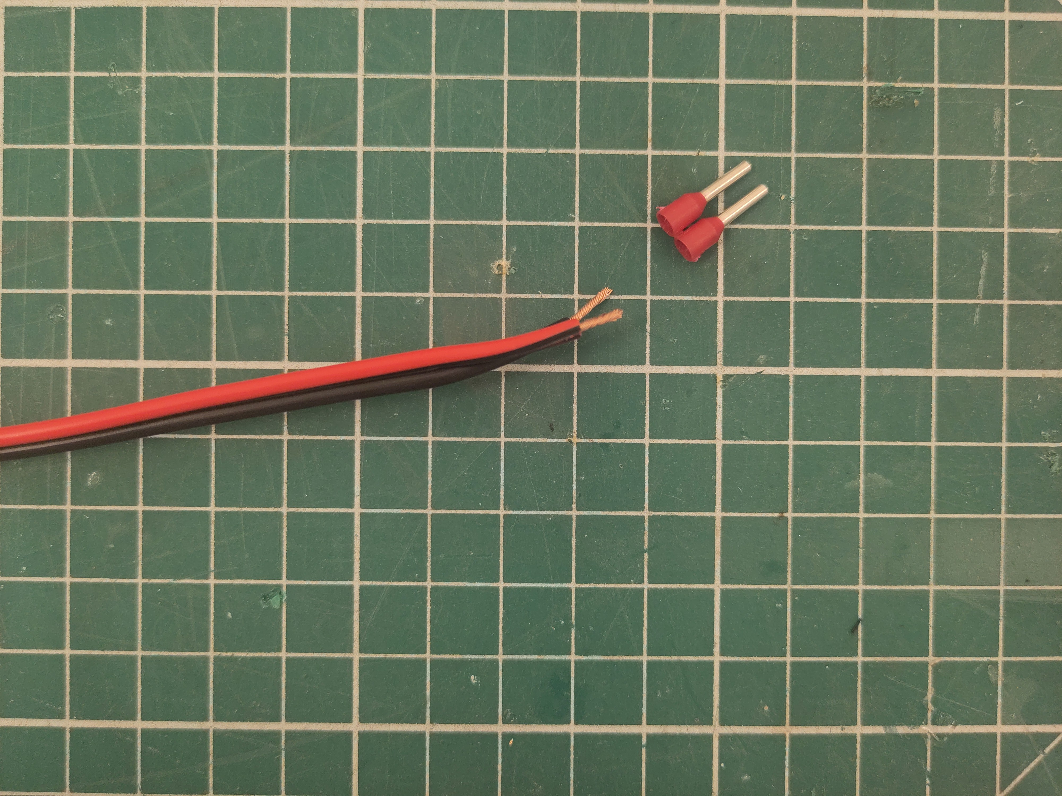
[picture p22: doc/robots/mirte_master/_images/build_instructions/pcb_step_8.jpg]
   
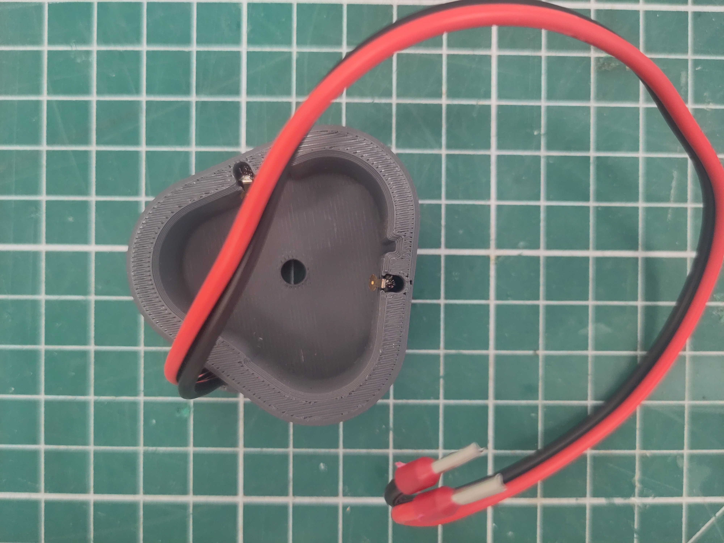
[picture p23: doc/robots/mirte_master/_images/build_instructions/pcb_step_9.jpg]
   

       ..

       Add the ferrules in order to finish the battery cap.

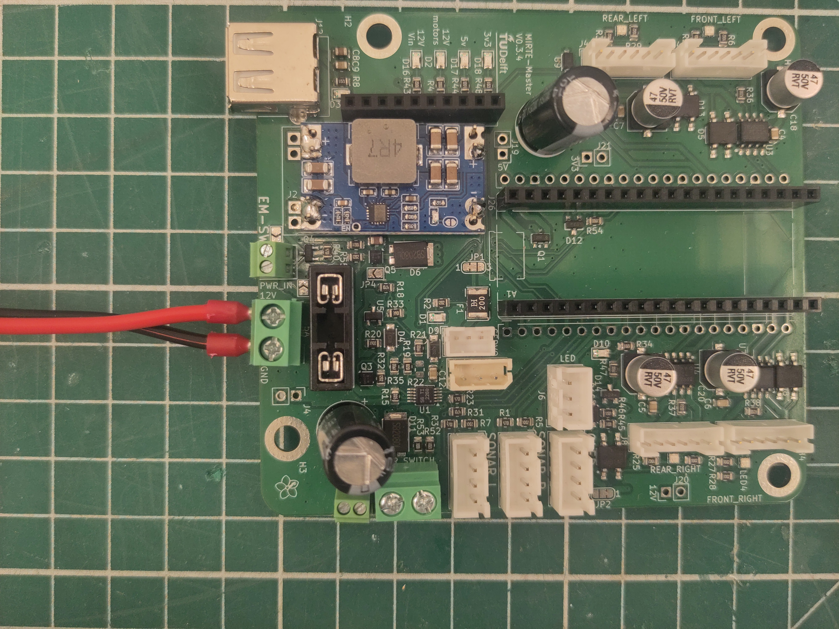
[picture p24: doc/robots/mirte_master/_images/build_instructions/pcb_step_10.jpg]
   

       ..

       Attach the battery cap to the PCB.

   
   

       ..

       Remove the green wire using a flat screwdriver.

   
   

       ..

       Notice the "NC" an "C" labels on the plug.

   

       ..

       And make sure to put the "NC" label where the green cable was.

   
   

       ..

       Add ferrules to the yellow and white wire.

   

       ..

       And connect the button wires to the PCB as seen in the picture.

   
   

       ..

       Add the blade fuse.

   
   

       ..

       Add the Raspberry Pi Pico.

   
   
 
       ..

       The PCB is already capable of having an emergency button attached. We do
       not use this yet. So we need to short this for now.

Servo settings
--------------

Before assembling the arm, please make sure that the servo's have the correct ID,
and are positioned in their 0 state. In order to do so, we have created a script 
that does this for each servo.

Each servo needs to be set seperately (so the servos can not be connected/daisy chained
with eachother). For this setup you should upload the right uf2 to the Raspberry Pi Pico,
You should now add the switch and the battery mount to the MIRTE PCB as on the 
picture below.

.. list-table::
   :header-rows: 1

   * - Servo
     - Type
     - ID
     - uf2
   * - Rotation
     - HX-12H
     - 2
     - `set_servo2.uf2 <https://github.com/ArendJan/mirte_set_serial_servos/releases/download/v2/set_servo_2.uf2>`_
   * - Shoulder
     - HTD-45H
     - 3
     - `set_servo3.uf2 <https://github.com/ArendJan/mirte_set_serial_servos/releases/download/v2/set_servo_3.uf2>`_
   * - Elbow
     - HTD-35H
     - 4
     - `set_servo4.uf2 <https://github.com/ArendJan/mirte_set_serial_servos/releases/download/v2/set_servo_4.uf2>`_
   * - Wrist
     - HX-12H
     - 5
     - `set_servo5.uf2 <https://github.com/ArendJan/mirte_set_serial_servos/releases/download/v2/set_servo_5.uf2>`_
   * - Gripper
     - HX-12H
     - 6
     - `set_servo6.uf2 <https://github.com/ArendJan/mirte_set_serial_servos/releases/download/v2/set_servo_6.uf2>`_

The steps you need to take for each servo are:

1) Upload the right uf2 to the Pico
2) Connect the servo to the PCB
3) Turn on the PCB by pressing the switch
4) Check if you saw the servo moving and/or validate by connecting the Pico to a (linux) pc 
   and read from serial: ``$ tio -b 115200 /dev/ttyACM0``

.. tip::

   When assembling multiple MIRTE Masters at once it makes sense to set all the servos 
   with the same ID. 

DC motor alignment
------------------

In order to assembe the MIRTE Master correctly, we need to maek sure that
the connector on the motor is roughtly on the same orentation as the motor
shaft. Unfortunately, not all motors have this setup. So for some we need
to change this orientation by rotating the gearbox.

.. carousel::
   :show_controls:
   :show_fade:
   :show_buttons_on_top:
   :show_captions_below:

   

       ..

       Orient the motors with their shaft down.

   

       ..

       Depending on your motors, you need to reorientate the shaft location.
       In this picture, only the left one is correct. The others need to be
       changed.

   

       ..

       Carefully disasseble the metal cover. The gearbox consists of all
       loose elements. Make sure to take the cover up as straight as 
       possible.

   

       ..

       Carefully remove the geabox, and unscrew the last plate.

   

       ..

       Put the gearbox back on the plate, and try to turn the plate/gearbox
       combo until it is roughtly in the right direction, and the screws of
       the plate are aligned with holes.

   

       ..

       Fix the plate in the right orientation.

   

       ..

       Put back the gearbox. Especially the brass stands might have misaligned
       a bit while doing so. Make sure to wobble the geabox carefully in order
       to realign the gearbox.

   
   

       ..

       Reattach the cover.

   

       ..

       All motors should have their connector roughly on the same side as the shaft.

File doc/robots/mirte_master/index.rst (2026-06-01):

MIRTE Master
=============

.. toctree::
   :maxdepth: 1
   :hidden:

   bom
   preparations
   build_instructions
   hardware_test
   calibration  

Upgrade your MIRTE robot to a full mobile manipulator. The robot
includes a depth camera and 2D lidar. You can control the robot
with Nav2 and MoveIt!



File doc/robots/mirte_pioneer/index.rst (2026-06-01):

MIRTE Pioneer
=============

.. toctree::
   :maxdepth: 1
   :hidden:

   bom
   build_instructions
   connecting_cables

Explore all robotic possibilities. By adding a computer one can use even more
sensors (camera, but even lidar) and a gripper. Apart from programming in blocks
and Python, one can also use all possibilites of Robot Operating System (ROS).



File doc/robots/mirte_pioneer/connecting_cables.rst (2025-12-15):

Connecting the Cables
#####################

Connecting the power
====================

.. tabs::

   .. group-tab:: MIRTE PCB

      You should connect the powerbank to the connector that is marked RED on the PCB.

      

      

       

Connecting the peripherals
==========================

The MIRTE PCB is nothing more than just a bunch of cables on a board. You can of
course also connect the same hardware to a breadboard. The fritzing image below 
shows you how to connect all the hardware in order to get the same pin layout
as the PCB. But you are also free to chose different pins and change the 
configuration later on.

.. tabs::

   .. group-tab:: MIRTE PCB

      You should connect the hardware to the connecter that is marked RED on the PCB.

      .. tabs::

         .. group-tab:: Motor

            

            

             

         .. group-tab:: Servo

            

            

             

         .. group-tab:: OLED

            

            

             

         .. group-tab:: Line follow

            

            

             

         .. group-tab:: Distance

            

            

             

   .. group-tab:: Pi Pico

     .. _pico-wiring:

     Alternative text

   .. group-tab:: Arduino Nano

     Alternative text

     .. note::
       Please note that:

       - The motors are now controlled with one PWM and one digital pin.
       - Two I2C OLED screens are only possible when you have two OLEDS with different addresses (either by default, or soldered).

   .. group-tab:: Arduino Uno

     Alternative text

     .. note::
       Please note that:

       - The motors are now controlled with one PWM and one digital pin.
       - Two I2C OLED screens are only possible when you have two OLEDS with different addresses (either by default, or soldered).
       - The digital value of the IR line sensor is not used.
       - The power of all peripherals (or at least the motor controller) needs to come from the breadboard power supply.

   .. group-tab:: STM32

      Alternative text

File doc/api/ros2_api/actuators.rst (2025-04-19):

:orphan:

Actuators
=========

.. .. include:: ros2_api/actuators/motors.rst

.. include:: ./actuators/oled.rst

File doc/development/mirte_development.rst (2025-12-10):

MIRTE Development
#################

As mentioned before we are currently still developing MIRTE. But the ultimate goal is to have a vibrant
community contributing to the project.

.. warning::
   Currently this isn't correct.
   Currently none of the interfaces (hardware, software) are definitive. This means that we might still
   change this. Developing educational material around MIRTE is possible, but you should be able to
   modify this in case we change the interfaces.

Building a custom SD image
==========================

The latest image can be downloaded from `the download site <https://github.com/mirte-robot/mirte-sd-image-tools/releases/latest>`_. For university
or maker level this might not fully do what you want in your course. In that case you can modify
the image yourself and add software or default settings. This can be done with the mirte-sd-image-tools.
Note that this can onlu be done on Linux machines.

1. Checkout the mirte-sd-image-tools:

   .. code-block:: bash

      $ git clone https://github.com/mirte-robot/mirte-sd-image-tools
      $ cd mirte-sd-image-tools

2. Install the prerequisites (`singularity container <https://sylabs.io/guides/3.0/user-guide/installation.html#install-the-debian-ubuntu-package-using-apt>`_ ) 
   preferably via apt.

3. Build the singularity image:

   .. code-block:: bash

      $ ./install.sh

4. Rename your downloaded version to mirte_orangepi_sd.img or mirte_raspberrypi_sd.img:

   .. code-block:: bash

      $ mv mirte_<timestamp>_orangepi_sd.img mirte_orangepi_sd.img

5. Resize the image to make space for extra software:

   .. code-block:: bash

      $ sudo singularity run --app prepare_image --bind ./mirte_orangepi_sd.img:/mirte_sd.img image_tools.sif

6. Chroot into the sd image:

   .. code-block:: bash

      $ ./run.sh image_shell orangepi

7. Run any command you think is needed to modify your image and exit when done.

8. You can shrink and xz the image again for distribution:

   .. code-block:: bash

      $ sudo singularity run --app shrink_image --bind ./mirte_orangepi_sd.img:/mirte_sd.img image_tools.sif
      $ xz -vT6 ./mirte_orangepi_sd.img

Development for Web Interface
=============================

Developing the Vue frontend on the orangepi might be tricky due to the limited RAM of the 
SBC. It therefore is advised to checkout the mirte-web-interface on your own machine
and develop there:

.. code-block:: bash

   $ git clone https://github.com/mirte-robot/mirte-web-interface
   $ cd mirte-web-interface
   $ sudo apt install -y python3-pip python3-setuptools python3-wheel
   $ sudo -H pip install nodeenv
   $ nodeenv --node=16.2.0 node_env
   $ source node_env/bin/activate
   (node_env)$ npm install .
   (node_env)$ npm serve

You can now access the web interface on http://localhost:4000. Since this is running locally
on your machine. Not everything might be working (eg. the connection to ROS). You can therefore
also build the frontend locally and upload it to the robot:

.. code-block:: bash

   $ npm run build && ssh mirte@mirte.local "rm -rf /usr/local/src/mirte/mirte-web-interface/vue-frontend/dist" && scp -r dist/ mirte@mirte.local:/usr/local/src/mirte/mirte-web-interface/vue-frontend

Adding another language
=======================

Multi lingual support is only available in the web interface and tutorials. We think children should
learn technology in their own language instead of having to learn a foreign language at the same time. 
At some point we do think students should be able to use English as a language to learn more about
technology. 

The main language is English and can be found the `frontend <https://github.com/mirte-robot/mirte-web-interface/blob/main/vue-frontend/locales/en.json>`_ 
code. Adding a language can be as simple as a pull request with another json file.

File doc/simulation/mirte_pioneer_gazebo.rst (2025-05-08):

MIRTE Pioneer
#############

MIRTE Pioneer in Gazebo Classic

To start the MIRTE Pioneer in simulation you can:

.. code-block:: bash

   $ ros2 launch mirte_gazebo gazebo_mirte_pioneer_robocupjunior.launch.xml

This will start the simulation, including the controller for the base.

Controlling the base
--------------------

To control the base, you can send a Twist message to the same cmd_vel
topic as on the physical MIRTE robot (/mirte_base_controller/cmd_vel_unstamped).
The easiest way of doing so, is using the teleop_twist_keyboard package:

.. code-block:: bash

   $ ros2 run teleop_twist_keyboard teleop_twist_keyboard --ros-args --remap cmd_vel:=/mirte_base_controller/cmd_vel_unstamped

.. note::

   In this setup we have added a fixed camera to the environment
   (/camera_top_down/image_raw). It will show the stream of the
   topdown view of the environment. This stream can be used for
   grading purposes and be combined in a CI.

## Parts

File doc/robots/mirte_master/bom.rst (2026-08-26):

Bill of Materials
#################

The MIRTE Master was designed to be the upgraded bigger brother of the MIRTE Pioneer. With
this the students can focus more on robot applications rather than the inner workings of
the robot. Like with the MIRTE Pioneer, we tried to minimize the number of custom components. 

With the MIRTE Master you can decide to build just the mobile base, the manipulator arm, or
both. Please find below the components you need for these.

.. warning::

   Currently we have only built the base, and both. The standalone arm is not yet finished.

.. warning::

   The hardes part to get your hands on is probably the custom MIRTE PCB. We will have a look
   at finding ways to easily order these. Ideas are more than welcome. For now, do not hesitate
   to contact us on `discord <https://discord.gg/T54MZTberQ>`_ to get discuss instructions.

.. tabs::

   .. group-tab:: Mobile base

      .. list-table::
        :widths: 5 45 50
        :header-rows: 1

        * - #
          - component
          - type
        * - 1
          - Computer
          - `Orange Pi 3B v2.1 <http://www.orangepi.org/html/hardWare/computerAndMicrocontrollers/details/Orange-Pi-3B.html>`_
        * - 1
          - eMMC (optional)
          - 32GB eMMC
        * - 1
          - micro SD card
          - Intenso 16Gb (class 10) micro SD card
        * - 1
          - Microcontroller
          - `Raspberry Pi Pico H (RP2040) <https://www.raspberrypi.com/products/raspberry-pi-pico/>`_
        * - 1
          - MIRTE Master PCB
          - `MIRTE Master main control PCB <https://github.com/mirte-robot/mirte-pcb/tree/main/mirte-master-bottom>`_   
        * - 1
          - OLED Screen
          - `white SSD1306 128x64 I2C <https://nl.aliexpress.com/item/1005007755490093.html>`_
        * - 4
          - DC motors (incl encoders)
          - `12V 107RPM JGB37-520 <https://nl.aliexpress.com/item/1005005021902364.html>`_
        * - 1
          - Mecanum wheel (set of 4)
          - `97mm (2 left, 2 right) <https://nl.aliexpress.com/item/1005007533099560.html>`_ [#f1]_
        * - 1
          - Depth Camera
          - `Orbbec Astra Mini Pro <https://www.orbbec.com/products/structured-light-camera/astra-series/>`_
        * - 1
          - 2D Lidar
          - `Slamtec rplidar C1 <https://www.seeedstudio.com/RPLiDAR-C1M1-R2-Portable-ToF-Laser-Scanner-Kit-12M-Range-p-5840.html>`_
        * - 2 
          - Ultrasonic sensor
          - `HC-SR04 <https://nl.aliexpress.com/item/32283526790.html>`_
        * - 1
          - IMU
          - `MPU-9250 <https://nl.aliexpress.com/item/1005009122504274.html>`_
        * - 1
          - Ethernet Extension cable
          - `Delock 25 cm <https://www.reichelt.com/nl/nl/shop/product/cat_6a_verlengkabel_s_ftp_zwart_0_25_m-317744>`_
        * - \-
          - 12KG.CM Servo
          - `HX-12H (12KG.CM) Servo <https://www.hiwonder.com/products/hx-12h>`_ [#f2]_
        * - \-
          - 35KG.CM Servo
          - `HTD-35H (35KG.CM) Servo <https://www.hiwonder.com/products/htd-35h>`_
        * - \-
          - 45KG.CM Servo
          - `HTD-45H (45KG.CM) Servo <https://www.hiwonder.com/products/htd-45h>`_ 
        * - \-
          - Ball bearing
          - `6812 2RS <https://nl.aliexpress.com/item/1005007420073930.html>`_
        * - \-
          - USB camera
          - `OV9726 <https://nl.aliexpress.com/item/1005008554975902.html>`_

   .. group-tab:: Mobile manipulator

     .. list-table::
        :widths: 5 45 50
        :header-rows: 1

        * - #
          - component
          - type
        * - 1
          - Computer
          - `Orange Pi 3B v2.1 <http://www.orangepi.org/html/hardWare/computerAndMicrocontrollers/details/Orange-Pi-3B.html>`_
        * - 1
          - eMMC (optional)
          - 32GB eMMC
        * - 1
          - micro SD card
          - Intenso 16Gb (class 10) micro SD card
        * - 1
          - Microcontroller
          - `Raspberry Pi Pico H (RP2040) <https://www.raspberrypi.com/products/raspberry-pi-pico/>`_
        * - 1
          - MIRTE Master PCB
          - `MIRTE Master main control PCB <https://github.com/mirte-robot/mirte-pcb/tree/main/mirte-master-bottom>`_   
        * - 1
          - OLED Screen
          - `white SSD1306 128x64 I2C <https://nl.aliexpress.com/item/1005007755490093.html>`_
        * - 4
          - DC motors (incl encoders)
          - `12V 107RPM JGB37-520 <https://nl.aliexpress.com/item/1005005021902364.html>`_
        * - 1
          - Mecanum wheel (set of 4)
          - `97mm (2 left, 2 right) <https://nl.aliexpress.com/item/1005007533099560.html>`_ [#f1]_
        * - 1
          - Depth Camera
          - `Orbbec Astra Mini Pro <https://www.orbbec.com/products/structured-light-camera/astra-series/>`_
        * - 1
          - 2D Lidar
          - `Slamtec rplidar C1 <https://www.seeedstudio.com/RPLiDAR-C1M1-R2-Portable-ToF-Laser-Scanner-Kit-12M-Range-p-5840.html>`_
        * - 2 
          - Ultrasonic sensor
          - `HC-SR04 <https://nl.aliexpress.com/item/32283526790.html>`_
        * - 1
          - IMU
          - `MPU-9250 <https://nl.aliexpress.com/item/1005009122504274.html>`_
        * - 1
          - Ethernet Extension cable
          - `Delock 25 cm <https://www.reichelt.com/nl/nl/shop/product/cat_6a_verlengkabel_s_ftp_zwart_0_25_m-317744>`_
        * - 3
          - 12KG.CM Servo
          - `HX-12H (12KG.CM) Servo <https://www.hiwonder.com/products/hx-12h>`_ [#f2]_
        * - 1
          - 35KG.CM Servo
          - `HTD-35H (35KG.CM) Servo <https://www.hiwonder.com/products/htd-35h>`_
        * - 1
          - 45KG.CM Servo
          - `HTD-45H (45KG.CM) Servo <https://www.hiwonder.com/products/htd-45h>`_ 
        * - 1
          - Ball bearing
          - `6812 2RS <https://nl.aliexpress.com/item/1005007420073930.html>`_
        * - 1
          - USB camera
          - `OV9726 <https://nl.aliexpress.com/item/1005008554975902.html>`_

Electronic components
---------------------

.. tabs::

   .. group-tab:: Mobile base

      .. list-table::
        :widths: 5 45 50
        :header-rows: 1

        * - #
          - component
          - type
        * - 1
          - switch
          - `switch <https://www.tinytronics.nl/nl/schakelaars/manuele-schakelaars/drukknoppen-en-schakelaars/metalen-drukknop-16mm-reset-met-3v-blauwe-led-verlichting>`_
        * - 1
          - 12-5V step down
          - `12-5V step down <https://nl.aliexpress.com/item/1005006721587257.html>`_
        * - 1
          - 5A Blade fuse
          - `5A Blade fuse <https://nl.rs-online.com/web/p/car-fuses/7874108>`_
        * - 1
          - battery
          - `Parkside Performance 12V, 5Ah <https://www.lidl.nl/p/parkside-performance-accu-12-v-5-ah/p100396693>`_
        * - 2
          - Spring contact
          - `Spring contact <https://nl.rs-online.com/web/p/grounding-contacts/7884880>`_
        * - 1
          - 20cm wire
          -

   .. group-tab:: Mobile manipulator

      .. list-table::
        :widths: 5 45 50
        :header-rows: 1

        * - #
          - component
          - type
        * - 1
          - switch
          - `switch <https://www.tinytronics.nl/nl/schakelaars/manuele-schakelaars/drukknoppen-en-schakelaars/metalen-drukknop-16mm-reset-met-3v-blauwe-led-verlichting>`_
        * - 1
          - 12-5V step down
          - `12-5V step down <https://nl.aliexpress.com/item/1005006721587257.html>`_
        * - 1
          - 5A Blade fuse
          - `5A Blade fuse <https://nl.rs-online.com/web/p/car-fuses/7874108>`_
        * - 1
          - battery
          - `Parkside Performance 12V, 5Ah <https://www.lidl.nl/p/parkside-performance-accu-12-v-5-ah/p100396693>`_
        * - 2
          - Spring contact
          - `Spring contact <https://nl.rs-online.com/web/p/grounding-contacts/7884880>`_
        * - 1
          - 20cm wire
          -

Cables
------

.. tabs::

   .. group-tab:: Mobile base

      .. list-table::
        :widths: 5 45 50
        :header-rows: 1

        * - #
          - component
          - usage
        * - 1
          - `JST XH cables 4 pins, double head, 10-20cm <https://nl.aliexpress.com/item/1005002179605258.html>`_
          - OLED screen
        * - 2
          - micro USB cable (USB A - USB B micro) 15 cm [#f3]_
          - Pico & RPLidar 
        * - 1
          - USB-C cable (USB A - USB C) 20 cm
          - Orange Pi 3B Power  
        * - 2
          - `JST XH cables 4 pins, double head, 30cm <https://nl.aliexpress.com/item/1005002179605258.html>`_
          - Ultrasonic sensor
        * - 2
          - `JST **PH** cable 6 pins, double head, 20cm <https://nl.aliexpress.com/item/1005006188790994.html>`_
          - DC front motors
        * - 2
          - `JST **PH** cable 6 pins, double head, 30cm <https://nl.aliexpress.com/item/1005006188790994.html>`_
          - DC rear motors

   .. group-tab:: Mobile manipulator

      .. list-table::
        :widths: 5 45 50
        :header-rows: 1

        * - #
          - component
          - usage
        * - 1
          - `JST XH cables 4 pins, double head, 10-20cm <https://nl.aliexpress.com/item/1005002179605258.html>`_
          - OLED screen
        * - 2
          - micro USB cable (USB A - USB B micro) 15 cm [#f3]_
          - Pico & RPLidar 
        * - 1
          - USB-C cable (USB A - USB C) 20 cm
          - Orange Pi 3B Power  
        * - 2
          - `JST XH cables 4 pins, double head, 30cm <https://nl.aliexpress.com/item/1005002179605258.html>`_
          - Ultrasonic sensor
        * - 2
          - `JST **PH** cable 6 pins, double head, 20cm <https://nl.aliexpress.com/item/1005006188790994.html>`_
          - DC front motors
        * - 2
          - `JST **PH** cable 6 pins, double head, 30cm <https://nl.aliexpress.com/item/1005006188790994.html>`_
          - DC rear motors

Mounting
--------

.. tabs::

   .. group-tab:: Mobile base

      .. list-table::
        :widths: 5 40 5 50
        :header-rows: 1

        * - #
          - component
          - #
          - usage
        * - 2
          - `standoff 10mm M2.5 female-female <https://nl.rs-online.com/web/p/standoffs/1842689>`_
          -
          - Orange Pi 3B to bottom plate
        * - 4
          - `standoff 25mm M4 female-female <https://nl.rs-online.com/web/p/standoffs/1058101>`_
          -
          - MIRTE PCB to bottom plate
        * - \-
          - `standoff 20mm M4 female-female <https://nl.rs-online.com/web/p/standoffs/1058094>`_
          -
          - Middle to top plate
        * - \-
          - `standoff 40mm M3 male-female <https://nl.rs-online.com/web/p/standoffs/0221184>`_
          -
          - Arm base to top plate
        * - 2
          - M2 x 20 screws
          -
          - Orbbec Astra Mini Pro to camera module
        * - 2
          - M2 nut
          -
          - Orbbec Astra Mini Pro to camera module
        * - 8
          - M2.5 x 6 screws
          -
          - 
        * - 
          - ,,
          - 4
          - Orange Pi 3B to bottom plate
        * - 
          - ,,
          - 4
          - Lidar to lidar mount
        * - 4
          - M2.5 x 12 screws
          -
          - Shoulder print to inner arm plate
        * - 4
          - M2.5 spring washer
          -
          - Orange Pi 3B to bottom plate
        * - 4
          - M2.5 washer (form a)
          -
          - 
        * - 
          - ,,
          - 4
          - Orange Pi 3B to bottom plate
        * - 
          - ,,
          - \-
          - Shoulder print to inner arm plate
        * - \-
          - M2.5 locknut
          -
          - Shoulder print to inner arm plate
        * - \-
          - M3 x 6 screws
          -
          - 
        * -
          - ,,
          - \-
          - Horn to rotation Servo
        * -
          - ,,
          - \-
          - USB camera to camera module
        * - 14
          - M3 x 12 screws
          -
          - 
        * - 
          - ,,
          - 2
          - Ethernet port to side panel
        * - 
          - ,,
          - 12
          - DC motor to motor module (3 per motor)
        * - \-
          - M3 x 14 screws
          -
          - Gripper
        * - 4
          - M3 x 16 screws
          -
          - 
        * -
          - ,,
          - 4
          - Battery to battery module
        * - 
          - ,,
          - \-
          - Gripper
        * - \-
          - M3 x 18 screws
          -
          - Arm plates to bearing
        * - 4
          - M3 x 20 screws
          -
          - 
        * -
          - ,,
          - \-
          - Gripper
        * -
          - ,,
          - 4
          - Wheels to motor
        * - \-
          - M3 x 30 screws
          -
          - Gripper
        * - \-
          - M3 locknut
          -
          - 
        * -
          - ,,
          - \-
          - Inner arm plates to bearing
        * -
          - ,,
          - \-
          - Gripper
        * - 
          - ,,
          - \-
          - Arm to top plate
        * - 4
          - M3 washer (form a)
          -
          - Wheels to motor
        * - 35
          - M4 x 12 screws
          -
          - 
        * - 
          - ,,
          - 16
          - Base side panels to plates
        * - 
          - ,,
          - 4
          - Depth camera module to plates
        * - 
          - ,,
          - 4
          - Sonar modules to plates
        * - 
          - ,,
          - 8
          - MIRTE PCB to bottom plate   
        * -
          - ,,
          - 3
          - Lidar mount to middle plate
        * - 
          - ,,
          - \-
          - Middle to Top plate
        * - 8
          - M4 x 16 screws 
          -
          - Motor module to bottom plate
        * - 8
          - M4 locknut
          -
          - Motor module to bottom plate
        * - 19
          - M4 U-clip captive nut
          -
          - 
        * - 
          - ,,
          - 8
          - Base side panels to plates
        * -
          - ,,
          - 4
          - Depth camera module to plates
        * - 
          - ,,
          - 4
          - Sonar modules to plates
        * - 
          - ,,
          - 3
          - Lidar mount to middle plate 
        * - 8
          - M4 spring washer
          -
          - MIRTE PCB to bottom plate   
        * - 4
          - M4 washer (form a)
          - 
          - MIRTE PCB to bottom plate

   .. group-tab:: Mobile manipulator

      .. list-table::
        :widths: 5 40 5 50
        :header-rows: 1

        * - #
          - component
          - #
          - usage
        * - 2
          - `standoff 10mm M2.5 female-female <https://nl.rs-online.com/web/p/standoffs/1842689>`_
          -
          - Orange Pi 3B to bottom plate
        * - 4
          - `standoff 25mm M4 female-female <https://nl.rs-online.com/web/p/standoffs/1058101>`_
          -
          - MIRTE PCB to bottom plate
        * - 4
          - `standoff 20mm M4 female-female <https://nl.rs-online.com/web/p/standoffs/1058094>`_
          -
          - Middle to top plate
        * - 3
          - `standoff 40mm M3 male-female <https://nl.rs-online.com/web/p/standoffs/0221184>`_
          -
          - Arm base to top plate
        * - 2
          - M2 x 20 screws
          -
          - Orbbec Astra Mini Pro to camera module
        * - 2
          - M2 nut
          -
          - Orbbec Astra Mini Pro to camera module
        * - 8
          - M2.5 x 6 screws
          -
          - 
        * - 
          - ,,
          - 4
          - Orange Pi 3B to bottom plate
        * - 
          - ,,
          - 4
          - Lidar to lidar mount
        * - 4
          - M2.5 x 12 screws
          -
          - Shoulder print to inner arm plate
        * - 4
          - M2.5 spring washer
          -
          - Orange Pi 3B to bottom plate
        * - 8
          - M2.5 washer (form a)
          -
          - 
        * - 
          - ,,
          - 4
          - Orange Pi 3B to bottom plate
        * - 
          - ,,
          - 4
          - Shoulder print to inner arm plate
        * - 4
          - M2.5 locknut
          -
          - Shoulder print to inner arm plate
        * - 5
          - M3 x 6 screws
          -
          - 
        * -
          - ,,
          - 1
          - Horn to rotation Servo
        * -
          - ,,
          - 4
          - USB camera to camera module
        * - 14
          - M3 x 12 screws
          -
          - 
        * - 
          - ,,
          - 2
          - Ethernet port to side panel
        * - 
          - ,,
          - 12
          - DC motor to motor module (3 per motor)
        * - 2
          - M3 x 14 screws
          -
          - Gripper
        * - 8
          - M3 x 16 screws
          -
          - 
        * -
          - ,,
          - 4
          - Battery to battery module
        * - 
          - ,,
          - 4
          - Gripper
        * - 6
          - M3 x 18 screws
          -
          - Arm plates to bearing
        * - 9
          - M3 x 20 screws
          -
          - 
        * -
          - ,,
          - 5
          - Gripper
        * -
          - ,,
          - 4
          - Wheels to motor
        * - 2
          - M3 x 30 screws
          -
          - Gripper
        * - 16
          - M3 locknut
          -
          - 
        * -
          - ,,
          - 3
          - Inner arm plates to bearing
        * -
          - ,,
          - 10
          - Gripper
        * - 
          - ,,
          - 3
          - Arm to top plate
        * - 4
          - M3 washer (form a)
          -
          - Wheels to motor
        * - 43
          - M4 x 12 screws
          -
          - 
        * - 
          - ,,
          - 16
          - Base side panels to plates
        * - 
          - ,,
          - 4
          - Depth camera module to plates
        * - 
          - ,,
          - 4
          - Sonar modules to plates
        * - 
          - ,,
          - 8
          - MIRTE PCB to bottom plate   
        * -
          - ,,
          - 3
          - Lidar mount to middle plate
        * - 
          - ,,
          - 8
          - Middle to Top plate
        * - 8
          - M4 x 16 screws 
          -
          - Motor module to bottom plate
        * - 8
          - M4 locknut
          -
          - Motor module to bottom plate
        * - 19
          - M4 U-clip captive nut
          -
          - 
        * - 
          - ,,
          - 8
          - Base side panels to plates
        * -
          - ,,
          - 4
          - Depth camera module to plates
        * - 
          - ,,
          - 4
          - Sonar modules to plates
        * - 
          - ,,
          - 3
          - Lidar mount to middle plate 
        * - 8
          - M4 spring washer
          -
          - MIRTE PCB to bottom plate   
        * - 4
          - M4 washer (form a)
          - 
          - MIRTE PCB to bottom plate

Lasercut parts
--------------

.. tabs::

   .. group-tab:: Mobile base

      .. list-table::
        :widths: 5 95
        :header-rows: 1

        * - #
          - component
        * - 1
          - `Bottom plate (3mm PMMA) <https://surfdrive.surf.nl/public.php/dav/files/Aj4w3wwbfrmnSmb/Cut%20Files/Bottom_plate.DXF>`_
        * - 1
          - `Middle plate (3mm PMMA) <https://surfdrive.surf.nl/public.php/dav/files/Aj4w3wwbfrmnSmb/Cut%20Files/Middle_plate.DXF>`_
        * - 1
          - `Top plate (3mm aluminum/stainless steel) <https://surfdrive.surf.nl/public.php/dav/files/Aj4w3wwbfrmnSmb/Cut%20Files/Top_plate.DXF>`_
        * - \-
          - `Arm Inner Bottom plate (1.5mm aluminum/stainless steel) <https://surfdrive.surf.nl/public.php/dav/files/Aj4w3wwbfrmnSmb/Cut%20Files/Arm_Inner_Bottom_Plate.DXF>`_
        * - \-
          - `Arm Inner Top plate (1.5mm aluminum/stainless steel) <https://surfdrive.surf.nl/public.php/dav/files/Aj4w3wwbfrmnSmb/Cut%20Files/Arm_Inner_Top_Plate.DXF>`_
        * - \-
          - `Arm Outer Bottom plate (1.5mm aluminum/stainless steel) <https://surfdrive.surf.nl/public.php/dav/files/Aj4w3wwbfrmnSmb/Cut%20Files/Arm_Outer_Bottom_Plate.DXF>`_
        * - \-
          - `Arm Outer Top plate (1.5mm aluminum/stainless steel) <https://surfdrive.surf.nl/public.php/dav/files/Aj4w3wwbfrmnSmb/Cut%20Files/Arm_Outer_Top_Plate.DXF>`_

   .. group-tab:: Mobile manipulator

      .. list-table::
        :widths: 5 95
        :header-rows: 1

        * - #
          - component
        * - 1
          - `Bottom plate (3mm PMMA) <https://surfdrive.surf.nl/public.php/dav/files/Aj4w3wwbfrmnSmb/Cut%20Files/Bottom_plate.DXF>`_
        * - 1
          - `Middle plate (3mm PMMA) <https://surfdrive.surf.nl/public.php/dav/files/Aj4w3wwbfrmnSmb/Cut%20Files/Middle_plate.DXF>`_
        * - 1
          - `Top plate (3mm aluminum/stainless steel) <https://surfdrive.surf.nl/public.php/dav/files/Aj4w3wwbfrmnSmb/Cut%20Files/Top_plate.DXF>`_
        * - 1
          - `Arm Inner Bottom plate (1.5mm aluminum/stainless steel) <https://surfdrive.surf.nl/public.php/dav/files/Aj4w3wwbfrmnSmb/Cut%20Files/Arm_Inner_Bottom_Plate.DXF>`_
        * - 1
          - `Arm Inner Top plate (1.5mm aluminum/stainless steel) <https://surfdrive.surf.nl/public.php/dav/files/Aj4w3wwbfrmnSmb/Cut%20Files/Arm_Inner_Top_Plate.DXF>`_
        * - 1
          - `Arm Outer Bottom plate (1.5mm aluminum/stainless steel) <https://surfdrive.surf.nl/public.php/dav/files/Aj4w3wwbfrmnSmb/Cut%20Files/Arm_Outer_Bottom_Plate.DXF>`_
        * - 1
          - `Arm Outer Top plate (1.5mm aluminum/stainless steel) <https://surfdrive.surf.nl/public.php/dav/files/Aj4w3wwbfrmnSmb/Cut%20Files/Arm_Outer_Top_Plate.DXF>`_

3D printed parts
----------------

The original 3D printed parts are based on the components menstioned above. Since you might
want to modify your MIRTE Master based on our needs (or capability of stocking the components), 
you might need to (slightly) modify these.

These designs do not need support. The total amount of PLA needed for a mpobile manipulator
is roughly 1 kg.

.. tabs::

   .. group-tab:: Mobile base

      .. list-table::
        :widths: 5 45 50
        :header-rows: 1

        * - #
          - component
          - instructions
        * -
          - Base
          -
        * - 4
          - `Motor module <https://surfdrive.surf.nl/public.php/dav/files/Aj4w3wwbfrmnSmb/Print%20Files/Step/Frame/motor_module.STEP>`_
          - 
        * - 1
          - `Left panel <https://surfdrive.surf.nl/public.php/dav/files/Aj4w3wwbfrmnSmb/Print%20Files/Step/Frame/Left-Sidepanel-Module-OPI3Bv2.1.STEP>`_
          -   
        * - 1
          - `Right panel <https://surfdrive.surf.nl/public.php/dav/files/Aj4w3wwbfrmnSmb/Print%20Files/Step/Frame/Right-Sidepanel-Module-Ethernet.STEP>`_
          -   
        * - 1
          - `Front panel <https://surfdrive.surf.nl/public.php/dav/files/Aj4w3wwbfrmnSmb/Print%20Files/Step/Frame/Camera-Module%20Astra.STEP>`_
          -   
        * - 1
          - `Left Sonar module <https://surfdrive.surf.nl/public.php/dav/files/Aj4w3wwbfrmnSmb/Print%20Files/Step/Frame/Left-Sonar-Module.STEP>`_
          -   
        * - 1
          - `Right Sonar module <https://surfdrive.surf.nl/public.php/dav/files/Aj4w3wwbfrmnSmb/Print%20Files/Step/Frame/Right-Sonar-Module.STEP>`_
          -   
        * - 1
          - `Battery module <https://surfdrive.surf.nl/public.php/dav/files/Aj4w3wwbfrmnSmb/Print%20Files/Step/Frame/Battery-Module.STEP>`_
          -   
        * - 1
          - `Lidar module <https://surfdrive.surf.nl/public.php/dav/files/Aj4w3wwbfrmnSmb/Print%20Files/Step/Internal/LiDar-Module.STEP>`_
          -   
        * - 1
          - `Battery mount <https://surfdrive.surf.nl/public.php/dav/files/Aj4w3wwbfrmnSmb/Print%20Files/Step/Internal/Battery-Mount.STEP>`_
          -  
        * - \-
          - `Cable tube <https://surfdrive.surf.nl/public.php/dav/files/Aj4w3wwbfrmnSmb/Print%20Files/Step/Internal/Cable-Tube.STEP>`_
          -   
        * -
          - Arm
          -
        * - \-
          - `Rotation Servo Mount <https://surfdrive.surf.nl/public.php/dav/files/Aj4w3wwbfrmnSmb/Print%20Files/Step/Arm/ZRotation-Servo-Mount.STEP>`_
          - 
        * - \-
          - `Shoulder <https://surfdrive.surf.nl/public.php/dav/files/Aj4w3wwbfrmnSmb/Print%20Files/Step/Arm/Shoulder.STEP>`_
          - 
        * - \-
          - `Forearm <https://surfdrive.surf.nl/public.php/dav/files/Aj4w3wwbfrmnSmb/Print%20Files/Step/Arm/Forearm.STEP>`_
          - 
        * - \-
          - `Upperarm <https://surfdrive.surf.nl/public.php/dav/files/Aj4w3wwbfrmnSmb/Print%20Files/Step/Arm/Upperarm.STEP>`_
          - 
        * - \-
          - `Wrist <https://surfdrive.surf.nl/public.php/dav/files/Aj4w3wwbfrmnSmb/Print%20Files/Step/Arm/Wrist.STEP>`_
          - 
        * - \-
          - `Camera mount <https://surfdrive.surf.nl/public.php/dav/files/Aj4w3wwbfrmnSmb/Print%20Files/Step/Arm/Camera-Mount.STEP>`_
          - 
        * -
          - Gripper
          -
        * - \-
          - `Top plate <https://surfdrive.surf.nl/public.php/dav/files/Aj4w3wwbfrmnSmb/Print%20Files/Step/Gripper/plate_top_plate.STEP>`_
          - 
        * - \-
          - `Bottom plate <https://surfdrive.surf.nl/public.php/dav/files/Aj4w3wwbfrmnSmb/Print%20Files/Step/Gripper/plate_bottom_plate.STEP>`_
          - 
        * - \-
          - `Link <https://surfdrive.surf.nl/public.php/dav/files/Aj4w3wwbfrmnSmb/Print%20Files/Step/Gripper/link.STEP>`_
          - 
        * - \-
          - `Geared link <https://surfdrive.surf.nl/public.php/dav/files/Aj4w3wwbfrmnSmb/Print%20Files/Step/Gripper/geared%20actuator%20link.STEP>`_
          - 
        * - \-
          - `Geared actuated link <https://surfdrive.surf.nl/public.php/dav/files/Aj4w3wwbfrmnSmb/Print%20Files/Step/Gripper/geared%20actuated%20link.STEP>`_
          - 
        * - \-
          - `Spacer <https://surfdrive.surf.nl/public.php/dav/files/Aj4w3wwbfrmnSmb/Print%20Files/Step/Gripper/front_spacer.STEP>`_
          - 
        * - \-
          - `Actuating link left <https://surfdrive.surf.nl/public.php/dav/files/Aj4w3wwbfrmnSmb/Print%20Files/Step/Gripper/actuating%20link_left_actuation_link.STEP>`_
          - 
        * - \-
          - `Actuating link right <https://surfdrive.surf.nl/public.php/dav/files/Aj4w3wwbfrmnSmb/Print%20Files/Step/Gripper/actuating%20link_right_actualtion_link.STEP>`_
          - 
        * - \-
          - `Left tip <https://surfdrive.surf.nl/public.php/dav/files/Aj4w3wwbfrmnSmb/Print%20Files/Step/Gripper/tip_left_tip.STEP>`_
          - 
        * - \-
          - `Right tip <https://surfdrive.surf.nl/public.php/dav/files/Aj4w3wwbfrmnSmb/Print%20Files/Step/Gripper/tip_right_tip.STEP>`_
          - 

   .. group-tab:: Mobile manipulator

      .. list-table::
        :widths: 5 45 50
        :header-rows: 1
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

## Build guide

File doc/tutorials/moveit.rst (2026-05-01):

MoveIt!
#########

MoveIt2 is already installed on the MIRTE Master. This tutorial includes
remotely controlling the arm using RViz from a remote computer, and 
basic control of the arm using the MoveIt2 Python API.

Installation 
============

The easiest way to move the arm and gripper is to use RViz. Since this is 
a GUI we need to run this from a remote machine/laptop in the same
network. For this, make sure you have ROS2 humble installed, and that you
have created a ROS2 workspace. We still need to install the MIRTE
MoveIt package:

.. tabs::

   .. group-tab:: From the robot

      The most safe way to do this is installing the package that is
      installed on the actual robot:

      .. code-block:: bash

         $ cd mirte_ws/src
         $ scp -r mirte@mirte.local:/usr/local/src/mirte/mirte-ros-packages .

   .. group-tab:: From github

      You can also install the latets MIRTE MoveIt package from github. This one might
      be out of sync with the software on the robot though:

      .. code-block:: bash

         $ cd mirte_ws/src
         $ git clone https://github.com/mirte-robot/mirte-ros-packages

And you need to make sure that your LC_NUMERIC is set to en_US.UTF-8:

.. code-block:: bash

   $ sudo update-locale LC_NUMERIC=en_US.UTF-8
   $ export LC_NUMERIC=en_US.UTF-8

Optionally, you can remove the unused ROS packages. This will make the
install, and build go much faster. Only do this as long as you have no
changes in these folders.

.. code-block:: bash

   $ cd mirte-ros-packages
   $ rm -r mirte_bringup/ mirte_telemetrix_cpp/ mirte_teleop/ mirte_test/ mirte_zenoh_setup/
   $ cd ../..

.. code-block:: bash

   $ rm mirte_msgs/COLCON_IGNORE
   $ rosdep install --from-paths src --ignore-src -r
   $ colcon build

Rviz
====

Now that we have installed the MIRTE MoveIt package, we can launch the setup:

.. code-block:: bash

   $ source install/setup.bash
   $ ros2 launch mirte_moveit_config mirte_moveit.launch.py

The MIRTE arm has two planning groups (mirte_arm, and mirte_gripper). You can now select
which planning group you want to use (eg. mirte_arm), and select a goal state. There are
couple of preset states (open/close for the mirte_gripper, and home for the mirte_arm).

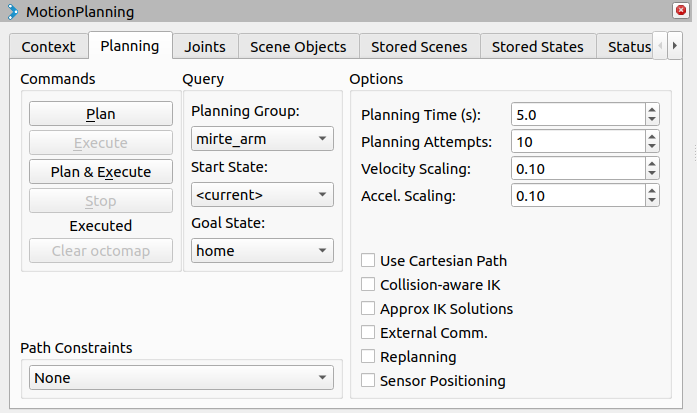
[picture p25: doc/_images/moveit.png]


By pressing "Plan & Excecute", the robot will execute the planned trajectory. For safety
reasons the default velocity and acceleration scaling is set to 0.10. You can change this
to 1.0 if you want the arm to move faster.

.. note::

   Due to the 4DOF nature of the arm, the blue selector in RViz is not usable.

MoveIt2 C++ API
==================

But of course the most usefull way to use MoveIt, is in your own code. This is why
there are C++ API for MoveIt. The example below will show you how to 
use this API to move the end effector of the robot to a certain position. Note that
this is a MIRTE modified version of the `MoveIt tutorial <https://moveit.picknik.ai/main/doc/tutorials/your_first_project/your_first_project.html>`_.

.. note::

   For later versions of ROS2, there is also a Python API.

The first this we need to do, is create a new C++ package:

.. code-block:: bash

   $ cd ~/mirte_ws/src
   $ ros2 pkg create --build-type ament_cmake --license Apache-2.0 --node-name moveit_example mirte_planning --dependencies rclcpp moveit_ros_planning_interface geometry_msgs

And modify the moveit_example node to:

.. code-block:: c++

   #include <memory>
   #include <thread>
   #include <rclcpp/rclcpp.hpp>
   #include <moveit/move_group_interface/move_group_interface.h>
   #include <geometry_msgs/msg/pose_stamped.hpp>

   int main(int argc, char * argv[])
   {
     // Initialize ROS and create the Node
     rclcpp::init(argc, argv);

     auto const node = std::make_shared<rclcpp::Node>(
       "moveit_node",
       rclcpp::NodeOptions().automatically_declare_parameters_from_overrides(true)
     );

     // Start spinning in a separate thread
     rclcpp::executors::SingleThreadedExecutor executor;
     executor.add_node(node);
     std::thread spinner([&executor]() {
       executor.spin();
     });

     // Wait for some initialization work
     rclcpp::sleep_for(std::chrono::seconds(2));

     // Create a ROS logger
     auto const logger = rclcpp::get_logger("moveit_node");

     // Create the MoveIt MoveGroup Interface
     using moveit::planning_interface::MoveGroupInterface;
     auto move_group_interface = MoveGroupInterface(node, "mirte_arm");

     // Set a target Pose
     auto const target_pose = []{
       geometry_msgs::msg::Pose msg;
       msg.position.x = 0.085;
       msg.position.y = 0.0;
       msg.position.z = 0.47;
       msg.orientation.x = 0.7;
       msg.orientation.y = 0.0;
       msg.orientation.z = 0.7;
       msg.orientation.w = 0.0;
       return msg;
     }();

     move_group_interface.setApproximateJointValueTarget(target_pose);

     // Or set to a named target
     //move_group_interface.setNamedTarget("home");

     // Create a plan to that target pose
     auto const [success, plan] = [&move_group_interface]{
       moveit::planning_interface::MoveGroupInterface::Plan msg;
       auto const ok = static_cast<bool>(move_group_interface.plan(msg));
       return std::make_pair(ok, msg);
     }();

     // Execute the plan
     if(success) {
       move_group_interface.execute(plan);
     } else {
       RCLCPP_ERROR(logger, "Planning failed!");
     }

     // Get the current pose of the end effector
     geometry_msgs::msg::PoseStamped current_pose = move_group_interface.getCurrentPose("wrist");

     // Print the current pose
     RCLCPP_INFO(rclcpp::get_logger("rclcpp"), "Current pose: position = [%f, %f, %f], orientation = [%f, %f, %f, %f]",
              current_pose.pose.position.x, current_pose.pose.position.y, current_pose.pose.position.z,
              current_pose.pose.orientation.x, current_pose.pose.orientation.y,
              current_pose.pose.orientation.z, current_pose.pose.orientation.w);

     // Shutdown ROS
     rclcpp::shutdown();
     spinner.join();
     return 0;
   }

And add a launchfile, that starts the MoveIt planner node as well:

.. code-block:: python

  from launch import LaunchDescription
  from launch_ros.actions import Node
  from moveit_configs_utils import MoveItConfigsBuilder

  def generate_launch_description():

    moveit_config = (
        MoveItConfigsBuilder("mirte")
        .robot_description(
            file_path="config/mirte_master.urdf.xacro",
        )
        .robot_description_semantic(file_path="config/mirte_master.srdf")
        .trajectory_execution(file_path="config/moveit_controllers.yaml")
        .planning_pipelines(
            pipelines=["ompl", "chomp", "pilz_industrial_motion_planner"]
        )
        .to_moveit_configs()
    )

    # Start the actual move_group node/action server
    move_group_node = Node(
        package="moveit_ros_move_group",
        executable="move_group",
        output="screen",
        parameters=[moveit_config.to_dict(), {"use_sim_time": False}],
        arguments=["--ros-args", "--log-level", "info"],
    )

    thing_node = Node(
            package='mirte_planning',
            executable='moveit_example',
            name='moveit_cpp_node',
            output='screen',
            parameters=[
              moveit_config.robot_description,
              moveit_config.robot_description_semantic,
              moveit_config.planning_pipelines,
              moveit_config.robot_description_kinematics,
            ],
    )

    return LaunchDescription([
       move_group_node,
       thing_node
    ])

From this point, you should be able to explore all option that MoveIt offers.

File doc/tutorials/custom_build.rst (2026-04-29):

Building a custom MIRTE
#######################

Apart from using one of our own MIRTE designs, you can of course also just
build your own robot or use MIRTE OS on an existing robot. In this
tutorial we will explain how to get started. Like with the robots from
the MIRTE family, you have to go through 4 steps:

1) Design and build the frame
2) Connect the electronics
3) Install the software
4) Configure the software

Design and build the frame
==========================

Designing a robot might be challenging. It is good to know the limitations 
of the MIRTE software so you can take that into account in your design.

Low level hardware
------------------
For the lower level hardware you can take a look at the :ref:`supported hardware
section <supported-hardware>` for the microcontroller peripherals. This includes 
DC motors (or actually different types of motor controllers). With that you 
should be able to control all types of DC motors through a motorcontroller.
Please take a look at the other peripheras (like servo's, and sensors) to 
see the limitations of each of them.

All these peripherals are communicating through our own implementation
of Telemetrix. Technically it is possible to add other peripherals. This
does involve implementing this on both the server- and client-side of 
Telemetrix.

Higher level hardware
---------------------

Depending on your application you can of course also include (depth) camera's
or 2D lidars though USB. Since the MIRTE stack runs on ROS, it is highly
advised to check if your hardware is supported by ROS. This makes integration
way easier.

Compute power
-------------

SBC
+++

The MIRTE OS is based on the Ubuntu flavor of `Armbian <https://armbian.com>`_. 
The easiest way to get MIRTE OS to work is using one of the supported SBCs:

- Orange Pi Zero 2
- Orange Pi 3b 
- Raspberry Pi 4/5

The closer you stay to this, the easier it will get.

+------------------------------------------------------------------------------------------+-----------------------+
| `Supported SBCs <https://github.com/mirte-robot/mirte-sd-image-tools/releases/latest>`_  | Easy                  |
+------------------------------------------------------------------------------------------+-----------------------+
| `Armbian supported SBCs <https://www.armbian.com/download/>`_                            | Moderately easy       |
+------------------------------------------------------------------------------------------+-----------------------+
| `Ubuntu machines <https://ubuntu.com/certified>`_                                        | Possible              |
+------------------------------------------------------------------------------------------+-----------------------+
| `Other ubuntu-like machines <https://distrowatch.com/search.php?basedon=Ubuntu>`_        | Hard                  |
+------------------------------------------------------------------------------------------+-----------------------+
| `Non-ubuntu Linux machines <https://distrowatch.com/>`_                                  | Really hard/imossible |
+------------------------------------------------------------------------------------------+-----------------------+
| Non-linux machines                                                                       | Impossible            |
+------------------------------------------------------------------------------------------+-----------------------+

MCU
+++

The MIRTE software stack is running Telemetrix to communicate to the lower
lever hardware. The default setup is using the Raspberry Pi Pico as MCU. 

We also support Arduino-based MCU's. So as long as your MCU supports the
Arduino SDK, it should be able to run our version of Telemetrix. You might
run into some issues though, due to possible limitations of the MCU.

Robot types
-----------

The design choices you make fully depend on your requirements. It might be
that you just want to slightly modify our design. But you can also design
a fully new type of robot.

Modified MIRTE robot
++++++++++++++++++++

The easiest way to get started is to (slightly) modify the base of one of 
the MIRTE robots. This can be useful if you just want to modify the location
of a sensor, want to use different motors, or want to use a different 
battery. 

**MIRTE Pioneer**: We used FreeCAD to create the MIRTE Pioneer so everyone
will be able to modify the original files. The files can be found
in the `mirte-frame <https://github.com/mirte-robot/mirte-frame>`_ 
repository.

**MIRTE Master**: We used Solidworks to create the MIRTE Master since this
is mostly used in a professional setting. But STEP files are also generated
to be used in other CAD-programs. You can find the files in the 
`mirte-master-frame <https://github.com/mirte-robot/mirte-master-frame>`_
repository.

Custom robot
++++++++++++

But of course you can also fully design an new MIRTE robot. For example an
outdoor, a boat, or a walking robot. By default you are able to use the ROS 
(and where available Python and Blockly) interfaces of each hardware peripheral. 
To also use the higher level capabilitiesof ROS (like Nav2 and/or MoveIt!) you 
should also create a URDF of your robot. 

It is good to know that the closer you stay to a differential or meccanum drive
mobile robot, the easier it is. Other drives (like Ackermann) can also be used
using ros2_controlm but still need some manual changes. The same thing holds
for the articulated arm.

Connect the electronics
=======================

Connecting all the hardware might be challenging, but is of course also part
of building your own robot. How to connect the cables, highly depends on the 
chose setup of your hardware peripherals. For reference you can have a look
at an :ref:`example setup <pico-wiring>`.

Your design can be a simple breadboard, a PCB (for example the MIRTE PCB), or
your own PCB design. You can also decide to use one of the MIRTE PCBs as
starting point. We used KiCad to design our PCBs, so everyone should be able
to modify our designs. The designs can be found in the `mirte_pcb
<https://github.com/mirte-robot/mirte-pcb>`_ repository.

Install the software
====================

After you have build and connected your robot, it is time to install the software.
This includes the MIRTE OS software for the computer, and our Telemetrix version
for the MCU.

Computer (SBC)
--------------

As menstioned earlier, installing the MIRTE OS can be done with different levels
of complexity. When sticking to one of the supported SBCs you can just :ref:`follow
the instructions <install_mirte_os>`.

If you want to use the MIRTE software on another SBC with Armbian support, you can 
create an image yourself using the `scripts we use <https://github.com/mirte-robot/mirte-sd-image-tools>`_
to build the default images.

In case you are not using an Arbian suported computer, you can also install
everyting yourself using our `install scripts <https://github.com/mirte-robot/mirte-install-scripts>`_.
Do note that you will probably run into some issues here, depending how close
your setup is to a regular Ubuntu system. This installation expects a Ubuntu 22.04
release.

Depending on your hardware choices and application, you might also need to install
some other ROS packages. Please note that these will probably not be exposed to 
the MIRTE Python API or MIRTE Blocky IDE.

Microcontroller (MCU)
---------------------

This should be similar to the regular :ref:`instructions <install_mirte_mcu>` on 
installing Telemetrix on the MCU.

Configure the robot
===================

Depending on the chosen hardware, you still need to configure the software in 
a way that it reflects your hardware. To do this you can follow the regular
instructions for :ref:`connecting to the robot <connect>`, and :ref:`accessing
the interface <access-interface>`.

To get the low level hardware to work, you need to update the settings for 
the robot. This can be done in the :ref:`regular way as well <Specify Hardware>`,
and can be done via the web interface or by modifying the yaml file.

This should get you a robot, which you can control through ROS (and for some
peripherals also Python and Blockly). This only controls the lower levels of the 
robot though. So you should be able to control the single motors, but you will
probably not be able to send Twist commands (and use Nav2) or use MoveIt!

In order for these to work, you need to create a URDF of your robot. Building
a URDF is outside the scope of this tutorial, but ou can find the URDFs of both 
MIRTE robots in the `mirte_description package 
<https://github.com/mirte-robot/mirte-ros-packages/tree/main/mirte_description>`_.

After having setup the URDF in the right way (correct names etc), you will 
probably also have to change the `ros2_control hardware interface 
<https://github.com/mirte-robot/mirte-ros-packages/tree/develop/mirte_control>`_.
These can be found here:

`MIRTE Pioneer base (differentail) ros2_control hardware interface 
<https://github.com/mirte-robot/mirte-ros-packages/tree/develop/mirte_control/mirte_pioneer_control/hardware>`_

`MIRTE Master base (meccanum) ros2_control hardware interface 
<https://github.com/mirte-robot/mirte-ros-packages/tree/develop/mirte_control/mirte_master_base_control/hardware>`_

`MIRTE Master arm (4 DOF) ros2_control hardware intreface 
<https://github.com/mirte-robot/mirte-ros-packages/tree/develop/mirte_control/mirte_master_arm_control/hardware>`_

After having done this, you should be able to have a functioning MIRTE robot.

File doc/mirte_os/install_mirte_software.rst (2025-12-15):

Installation
############

For the MIRTE Pioneer or MIRTE Master to work we need to install software on both the SD card and the microcontroller.
It might be useful to do this before fully assembling the robot. But it can also be done at a later stage.

.. _install_mirte_os:

Install MIRTE OS image
======================

.. tabs::

  .. group-tab:: MIRTE Pioneer

    The MIRTE Pioneer uses the Orange Pi Zero2. So we need to download the correct image:

    1. Download the latest SD card image `here <https://github.com/mirte-robot/mirte-sd-image-tools/releases/latest>`_ (mirte_orangepizero2.img.xz).
    2. Burn the image onto the SD card with for example `Balena Etcher <https://www.balena.io/etcher/>`_.
    3. Put the SD card in the Orange Pi Zero 2.

    

    The SD image will have two partitions. One containing the MIRTE software, which is read-only and serves as an overlayfs lower folder. The other one
    will be expanded to the max size and serves as an upper folder for overlayfs. This measn that all your work/changes will be stored in that partition.

  .. group-tab:: MIRTE Master

    The MIRTE Master uses the Orange Pi 3B. This board can be extended with eMMC memory. You can install the MIRTE OS
    on an SD card, or on eMMC.

    .. tabs::

      .. tab:: SD

        1. Download the latest SD card image `here <https://github.com/mirte-robot/mirte-sd-image-tools/releases/latest>`_ (mirte_master_mirte_orangepi3b.img.xz).
        2. Burn the image onto the SD card with for example `Balena Etcher <https://www.balena.io/etcher/>`_.
        3. Put the SD card in the Orange Pi 3B.

        

        The SD image will have two partitions. One containing the MIRTE software, which is read-only and serves as an overlayfs lower folder. The other one
        will be expanded to the max size and serves as an upper folder for overlayfs. This measn that all your work/changes will be stored in that partition.

      .. tab:: eMMC

        1. Download the latest SD card image `here <https://github.com/mirte-robot/mirte-sd-image-tools/releases/latest>`_ (mirte_master_installer_orangepi3b.img.xz).
        2. Burn the image onto the SD card with for example `Balena Etcher <https://www.balena.io/etcher/>`_.
        3. Put the SD card in the Orange Pi 3B.
        4. Boot the Orange Pi 3B, and wait approximately 20 min until the robot shuts off.
        5. Remove the SD card.

        

        The MIRTE software will be installed on the eMMC. This will be read-only and serve as the lower overlayfs folder. It makes sense to have an
        SD card with an empty overlayfs partition to store all your work/changes. This is the overlay_image download.

  .. tab:: Custom SBC

    Currently we support images for the Orange Pi Zero 2 (MIRTE Pioneer), Orange Pi 3B (MIRTE Master), and the Raspberry Pi.
    Depending on you hardware you can run the MIRTE OS from an SD card, or from eMMC.

    .. tabs::

      .. tab:: SD

        1. Download the latest SD card image for your hardware `here <https://github.com/mirte-robot/mirte-sd-image-tools/releases/latest>`_.
        2. Burn the image onto the SD card with for example `Balena Etcher <https://www.balena.io/etcher/>`_.
        3. Put the SD card in your SBC.

        

        The SD image will have two partitions. One containing the MIRTE software, which is read-only and serves as an overlayfs lower folder. The other one
        will be expanded to the max size and serves as an upper folder for overlayfs. This measn that all your work/changes will be stored in that partition.

      .. tab:: eMMC

        1. Download the latest SD card image for your hardware `here <https://github.com/mirte-robot/mirte-sd-image-tools/releases/latest>`_.
        2. Burn the image onto the SD card with for example `Balena Etcher <https://www.balena.io/etcher/>`_.
        3. Put the SD card in your SBC
        4. Boot the Orange Pi 3B, and wait until the robot shuts off (this can take some time. eg 20 mins on the MIRTE Master).
        5. Remove the SD card.

        

        The MIRTE software will be installed on the eMMC. This will be read-only and serve as the lower overlayfs folder. It makes sense to have an
        SD card with an empty overlayfs partition to store all your work/changes. This is the overlay_image download.

.. _install_mirte_mcu:

Install MCU software
====================

The MIRTE OS software needs to communicate (via Telemetrix) with the microcontroller (MCU).
One therefore also need to install this onto the MCU.

.. tabs::

  .. group-tab:: MIRTE Pioneer

     1. Download the latest uf2 with the MIRTE version of Telemetrix `here <https://github.com/mirte-robot/mirte-sd-image-tools/releases/latest>`_ (Telemetrix4RpiPico.uf2).
     2. Connect the Pico to you computer using a (data) USB cable while pressing the BOOTSEL button.
     3. Copy the uf2 file to the mass storage device called RPI_RP2.

  .. group-tab:: MIRTE Master

     These instructions assume you have the Raspberry Pi Pico connected to the OrangePi 3B via
     USB, and have installed MIRTE OS on the OrangePi 3B. Login to a terminal on the OrangePi 3B
     and:

     .. code-block:: bash

        mirte$ cd /usr/local/src/mirte/mirte-install-scripts
        mirte$ ./run_arduino.sh upload_pico

  .. tab:: Custom MCU

     Currently this step is only needed for the Raspberry Pi Pico, which is
     the default MCU for MIRTE. When using a Raspberry Pi Pico, you can follow
     the instructions of the MIRTE Pioneer. Instructions on installing this for
     other MCUs can be found :ref:`here <Using another MCU>`.

Installed Software
==================

After installing your MIRTE OS v0.2 image you will have a robot running:

+------------------+---------+--------+--------+--------+
| SBC              | Armbian | Ubuntu | kernel | ROS    |
+==================+=========+========+========+========+
| Orange Pi Zero 2 | 25.2.3  | 22.04  | 6.6.62 | Humble |
+------------------+---------+--------+--------+--------+
| Orange Pi 3b     | 25.2.3  | 22.04  | 6.13.3 | Humble |
+------------------+---------+--------+--------+--------+
| Raspberry Pi 3/4 | 24.8.1  | 22.04  | 6.6.45 | Humble |
+------------------+---------+--------+--------+--------+

Updating Software
=================

Updating the software currently means reinstalling the software: downloading
the newest software image, and installing it on an SD-card. Please note that
you will lose your own work done on the MIRTE if you use the same SD-card as
before. 

After re-installation you might also need to update the software on the MCU.
If your current version of the MIRTE Telemetrix on the MCU is relatively new,
this step will be easy.

.. tabs::

  .. group-tab:: MIRTE Pioneer

     These instructions assume you have the Raspberry Pi Pico connected to the OrangePi Zero2 via
     the MIRTE PBC, and have installed MIRTE OS on the OrangePi Zero2. Login to a terminal on the 
     OrangePi and:

     .. code-block:: bash

        mirte$ cd /usr/local/src/mirte/mirte-install-scripts
        mirte$ ./run_arduino.sh upload_pico
        mirte$ ./run_arduino.sh upload_pico # need to do this twice (known issue)

     If this does not work (even after the second try), you will probably have an older
     version of the Telemetrix software installed which is not able to update on the PCB.
     Please follow the instructions above to upload the new software.

  .. group-tab:: MIRTE Master

     These instructions assume you have the Raspberry Pi Pico connected to the OrangePi 3B via
     USB, and have installed MIRTE OS on the OrangePi 3B. Login to a terminal on the OrangePi 3B
     and:

     .. code-block:: bash

        mirte$ cd /usr/local/src/mirte/mirte-install-scripts
        mirte$ ./run_arduino.sh upload_pico

  .. tab:: Custom MCU

     Currently this step is only needed for the Raspberry Pi Pico, which is
     the default MCU for MIRTE. When using a Raspberry Pi Pico, you can follow
     the instructions of the MIRTE Pioneer. Instructions on installing this for
     other MCUs can be found :ref:`here <Using another MCU>`.

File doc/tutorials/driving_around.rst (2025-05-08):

Driving around
##############

.. warning::

   Currently the robot is controllable via multiple interfaces. At the moment
   this does assume you have two motors called 'left' and 'right'. Please
   make sure that your :ref:`settings are correct <DC Motor>`.

From web interface
==================

The robot can be controller from the web interface by goin to the 'control' tab:

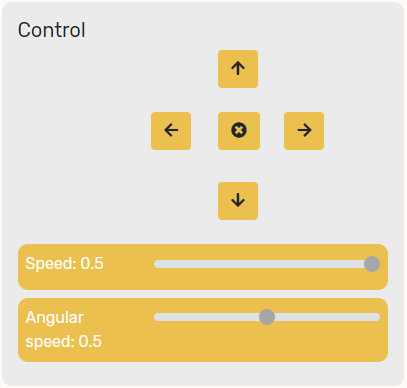
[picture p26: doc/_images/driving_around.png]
Driving around from the web interface
      

Teleop Key
==========

In ROS you can also drive around with your keyboard:

.. code-block:: bash

    mirte$ ros2 launch mirte_teleop teleop_key.launch.py

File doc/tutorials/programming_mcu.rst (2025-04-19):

:orphan:

Programming the MCU
###################

Instead of using the full MIRTE architecture including ROS, python and blockly, you
can also only program on the MCU. Where the standard MIRTE software using telemetrix
is making the MCU a dumb slave, this setup will make your SBC a dumb slave. One option
of course is to connect your MCU to your own computer. This section covers some 
options to program the MCU from your computer over the air (wireless) where the
SBC is just a wifi spot to your MCU.

.. warning::

   When reprogramming the MCU (and thus removing telemetrix from the MCU) all other
   features of MIRTE will not work anymore. You will only be able to control the
   robot through the MCU code. You can of course always get back to the original 
   situation by :ref:`preparing the microcontroller<Prepare microcontroller>` again.

.. note::

   Uploading to the MCU might fail. Especially the STM32 is quite picky on the code
   that will be uploaded to the MCU (for example 'PC_13' instead of 'PC13'). This means
   that the DFU upload over USB might not work. When this fails, you cal also try to 
   press the physical reset button on the MCU at the moment the upload should start.

Upload from terminal
====================

You can create your own projects in the arduino_project folder. This is also where
the Telemetrix code is stored, and an example Blink program. In order to create 
your own arduino project you can:

.. tabs::

   .. group-tab:: STM32

      .. code-block:: bash

          mirte$ cd ~/arduino_project/
          mirte$ mkdir MyFirstProject
          mirte$ cp Blink/Blink.ino MyFirstProject/MyFirstProject.ino
          mirte$ cd /usr/local/src/mirte/mirte_install_scripts/
          mirte$ ./run_arduino.sh build MyFirstProject
          mirte$ ./run_arduino.sh upload MyFirstProject

   .. group-tab:: Arduino Nano

      .. code-block:: bash

          mirte$ cd ~/arduino_project/
          mirte$ mkdir MyFirstProject
          mirte$ cp Blink/Blink.ino MyFirstProject/MyFirstProject.ino
          mirte$ cd /usr/local/src/mirte/mirte_install_scripts/
          mirte$ ./run_arduino.sh build_nano MyFirstProject
          mirte$ ./run_arduino.sh upload_nano MyFirstProject

   .. group-tab:: Arduino Nano (old)

      .. code-block:: bash

          mirte$ cd ~/arduino_project/
          mirte$ mkdir MyFirstProject
          mirte$ cp Blink/Blink.ino MyFirstProject/MyFirstProject.ino
          mirte$ cd /usr/local/src/mirte/mirte_install_scripts/
          mirte$ ./run_arduino.sh build_nano_old MyFirstProject
          mirte$ ./run_arduino.sh upload_nano_old MyFirstProject

   .. group-tab:: Arduino Uno

      .. code-block:: bash

          mirte$ cd ~/arduino_project/
          mirte$ mkdir MyFirstProject
          mirte$ cp Blink/Blink.ino MyFirstProject/MyFirstProject.ino
          mirte$ cd /usr/local/src/mirte/mirte_install_scripts/
          mirte$ ./run_arduino.sh build_uno MyFirstProject
          mirte$ ./run_arduino.sh upload_uno MyFirstProject

.. note:: 

   Compiling on the Orange Pi Zero might be really really slow.

Using Platform IO
=================

If you like a faster compilation time and/or like to develop from an IDE,
you can also develop your code using Platform IO. Make sure you have installed
Platform IO for your `IDE <https://docs.platformio.org/en/latest/integration/ide/index.html#desktop-ides>`_.

The next steps assume you have installed `VS Code <https://code.visualstudio.com/download>`_ 
with `Platform IO <https://platformio.org/install/ide?install=vscode>`_.

1. Create a new project by following the first two steps as described `here <https://docs.platformio.org/en/latest/integration/ide/vscode.html#setting-up-the-project>`_.
   You can still use the Arduino Uno in the example, you will override this later.
2. Replace the existing platformio.ini file of your project with the one below (replace
   <mirte_ip_address> with the IP address of your robot.
3. Start coding in main.cpp

.. tabs::

   .. group-tab:: STM32

      .. code-block:: ini

        [env:genericSTM32F103C8]
        platform = ststm32
        board = genericSTM32F103C8
        framework = arduino
        upload_protocol = custom
        upload_command = scp $SOURCE mirte@<mirte_ip_address>: && ssh mirte@<mirte_ip_address> /usr/bin/run-avrdude upload
        ; build flags needed due to bug: https://community.platformio.org/t/difficulty-with-getting-usb-serial-usb-cdc-working/7501/6
        ; AND to compensate for not using upload_protocol dfu
        build_unflags = -Wl,--defsym=LD_FLASH_OFFSET=0x0
        build_flags = 
          	-D PIO_FRAMEWORK_ARDUINO_ENABLE_CDC
	         -D USBCON
	         -D USBD_VID=0x0483
	         -D USBD_PID=0x5740
	         -D USB_MANUFACTURER="STMicroelectronics"
	         -D USB_PRODUCT="\"BLACKPILL_F103C8 CDC in FS Mode\""
	         -D HAL_PCD_MODULE_ENABLED
	         -D BL_LEGACY_LEAF 
	         -D VECT_TAB_OFFSET=0x2000
	         -Wl,--defsym=LD_FLASH_OFFSET=0x2000

   .. group-tab:: Arduino Nano

      .. code-block:: ini

        [env:nanoatmega328new]
        platform = atmelavr
        board = nanoatmega328new
        framework = arduino
        upload_protocol = custom
        upload_command = scp $SOURCE mirte@<mirte_ip_address>: && ssh mirte@<mirte_ip_address> /usr/bin/run-avrdude upload

   .. group-tab:: Arduino Nano (old)

      .. code-block:: ini

        [env:nanoatmega328]
        platform = atmelavr
        board = nanoatmega328
        framework = arduino
        upload_protocol = custom
        upload_command = scp $SOURCE mirte@<mirte_ip_address>: && ssh mirte@<mirte_ip_address> /usr/bin/run-avrdude upload

   .. group-tab:: Arduino Uno

      .. code-block:: ini

        [env:uno]
        platform = atmelavr
        board = uno
        framework = arduino
        upload_protocol = custom
        upload_command = scp $SOURCE mirte@<mirte_ip_address>: && ssh mirte@<mirte_ip_address> /usr/bin/run-avrdude upload

.. note::

   PlatformIO will ssh/scp into MIRTE two times asking for your password. It might be useful
   to create a setup where you login :ref:`using SSH keys <Keybased SSH login>`.

Using the Arduino IDE
=====================

.. warning::

   Uploading over the air with Arduino IDE is not perfect. For one it uses mDNS which is not
   supported by Windows 10. It also requires root login on the SBC which is far from optimal.
   We therefore might decide on removing this feature, so be careful when using this in
   any educational material.

The Arduino IDE should be configured in the same way as if the MCU was connected to the PC through USB. For the STM this means:

1. Add 'https://github.com/stm32duino/BoardManagerFiles/raw/master/STM32/package_stm_index.json' to 'File' > 'Settings' > 'Additional Boards Manager URLs'
2. Install 'STM32 Cores' from 'Tools' > 'Board: xxxx' > 'Boards Manager...'
3. Select 'Generic STM32F1 series' as 'Board', and make sure the other settings are as in the image below.
4. Compile and run will compile locally and upload the hex to MIRTE (passwd: mirte_mirte)

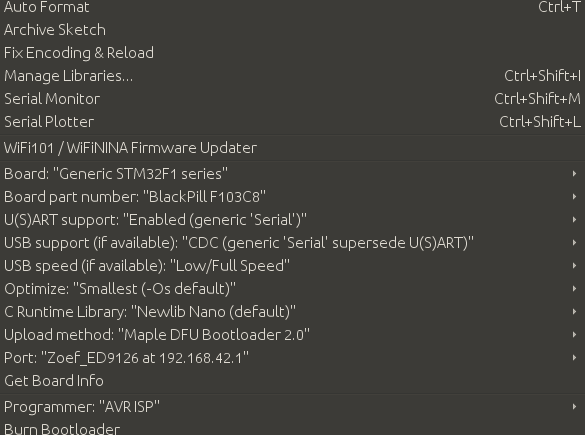
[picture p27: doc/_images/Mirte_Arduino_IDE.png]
MIRTE Arduino IDE


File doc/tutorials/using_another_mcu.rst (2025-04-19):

Using another MCU
#################

Prepare microcontroller
=======================

As mentioned during the :ref:`software installation <Installation>` the MIRTE robot needs
some software on the microcontroller to work. MIRTE uses a modified version of the Telemetrix 
protocol for this. This step is only needed when you have another MCU then the Raspberry Pi
Pico (i.e. STM32, Arduino Nano, or Arduino Uno).

From the terminal you can upload Telemetrix by executing:

.. code-block:: bash

    mirte$ cd /usr/local/src/mirte/mirte-install-scripts
    mirte$ ./run_arduino.sh upload_stm32 Telemetrix4Arduino

You can also upload to Arduino Nano (both new and old bootloader) and Arduino Uno. In that 
case replace 'upload_stm32' with 'upload_nano', 'upload_nano_old', or 'upload_uno'.

After this one still needs to configure the robot to match the pins of the MCU as
described in :ref:`Configure MIRTE<Configure MIRTE>`.

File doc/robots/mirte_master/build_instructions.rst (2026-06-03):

:orphan:

Build instructions
##################

.. carousel::
   :show_controls:
   :show_fade:
   :show_buttons_on_top:
   :show_captions_below:

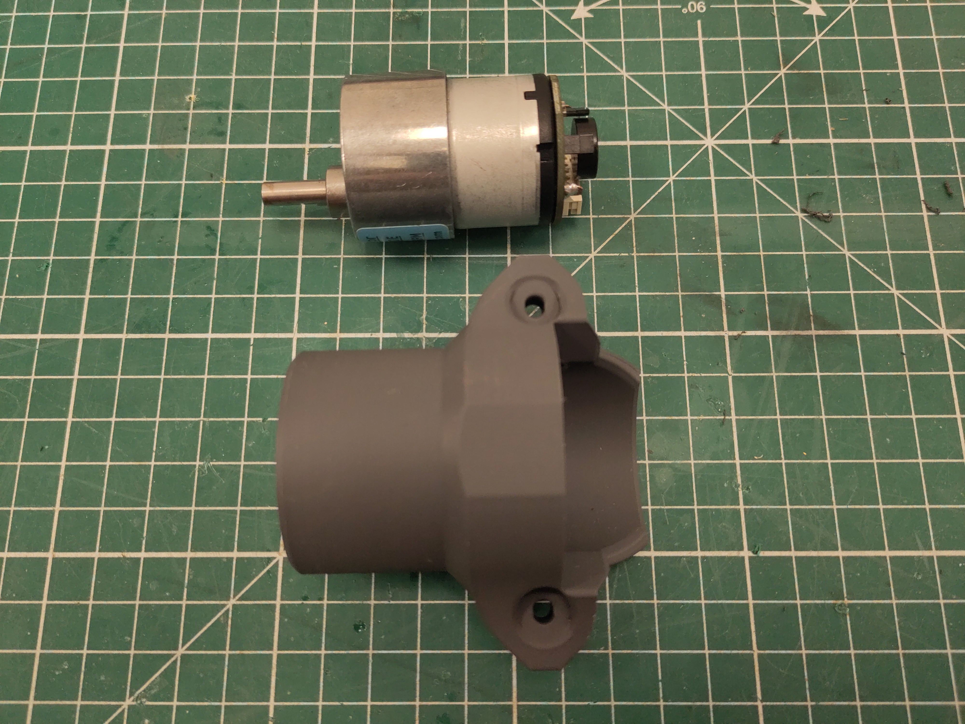
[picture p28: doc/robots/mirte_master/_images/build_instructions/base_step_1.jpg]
   
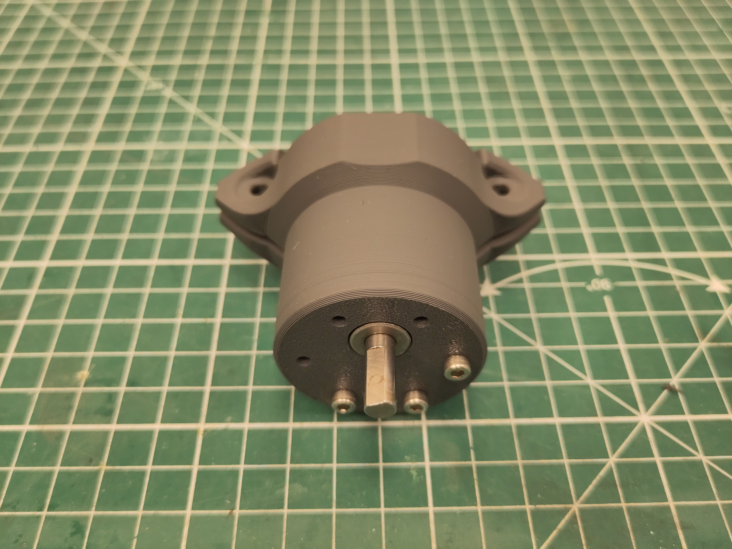
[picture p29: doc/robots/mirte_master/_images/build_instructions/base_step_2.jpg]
   

       ..

       Use the M3 x 12 screw to fix the motor. Make sure to use the
       three holes as shown otherwise the screw will block the
       gearbox.

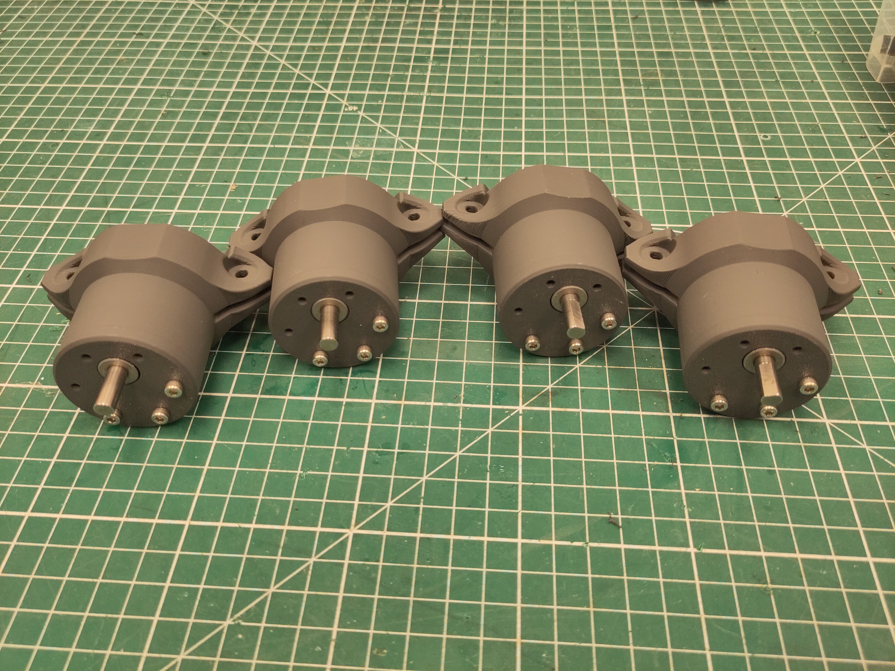
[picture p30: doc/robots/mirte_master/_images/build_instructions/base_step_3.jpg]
   
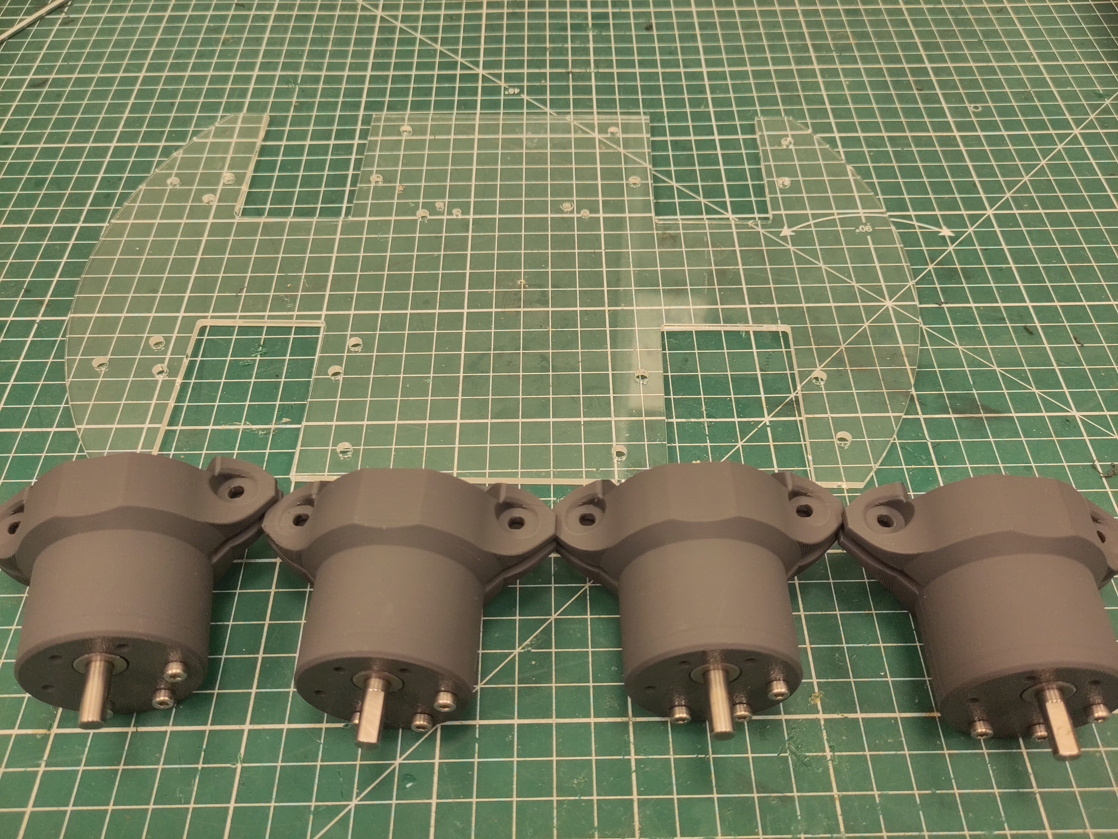
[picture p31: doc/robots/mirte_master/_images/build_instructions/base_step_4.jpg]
   
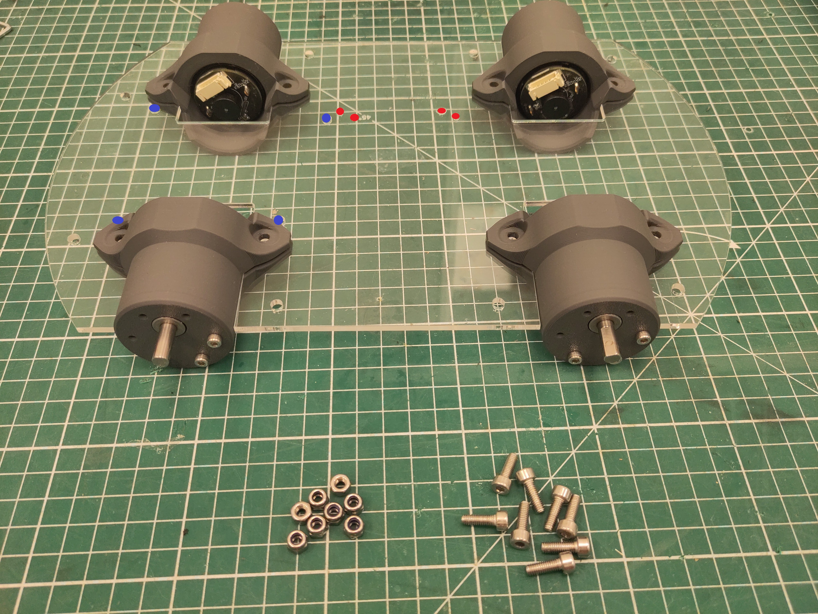
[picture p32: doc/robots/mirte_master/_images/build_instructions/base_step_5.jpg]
   

       ..

       Slide the motors in place. Make sure the orientation of the plate
       is correct, by looking at the holes of the PCB (blue) and OrangePi 
       (red). Use the M4 x 16 screws and M4 locknut to tighten the motors.

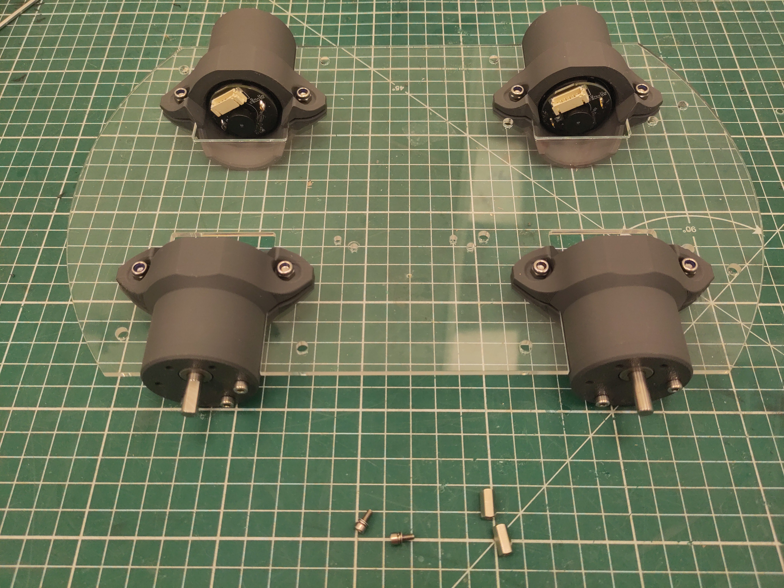
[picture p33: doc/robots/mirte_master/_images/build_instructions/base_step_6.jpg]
   

       ..

       Use the M2.5 standoff and M2.5 x 6 screws (with washer and spring
       washer).

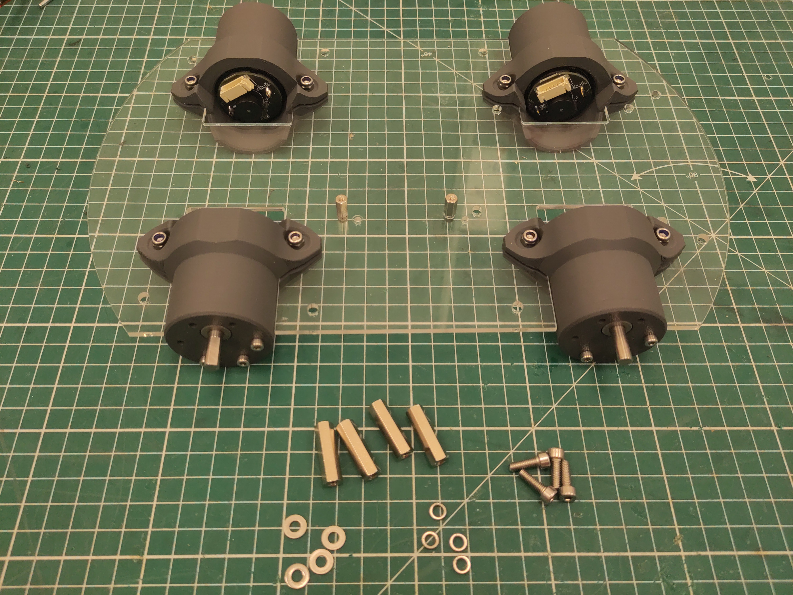
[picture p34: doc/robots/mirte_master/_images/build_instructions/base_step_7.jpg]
   

       ..

       Use the 25mm M4 standoff and M4 x 16 screws (with washer and spring
       washer).

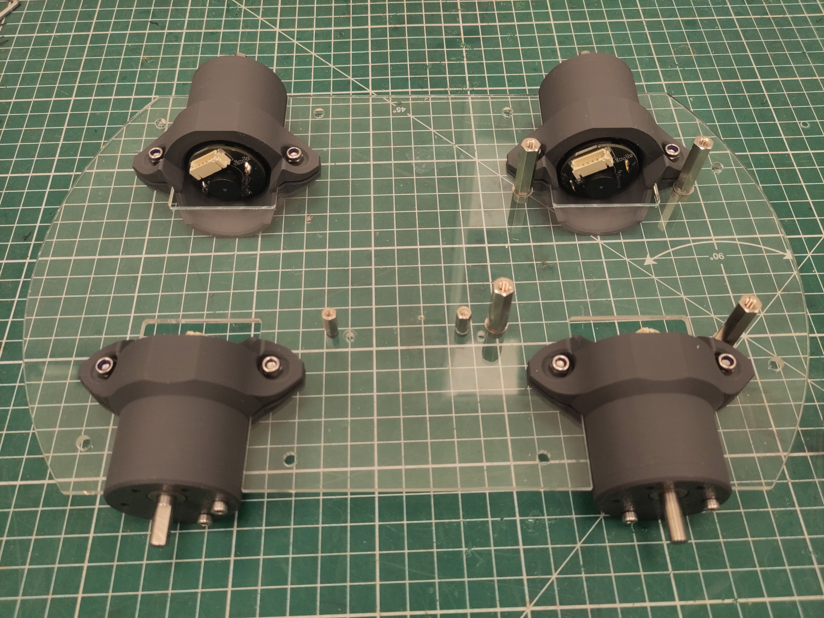
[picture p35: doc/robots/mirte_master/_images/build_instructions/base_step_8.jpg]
   
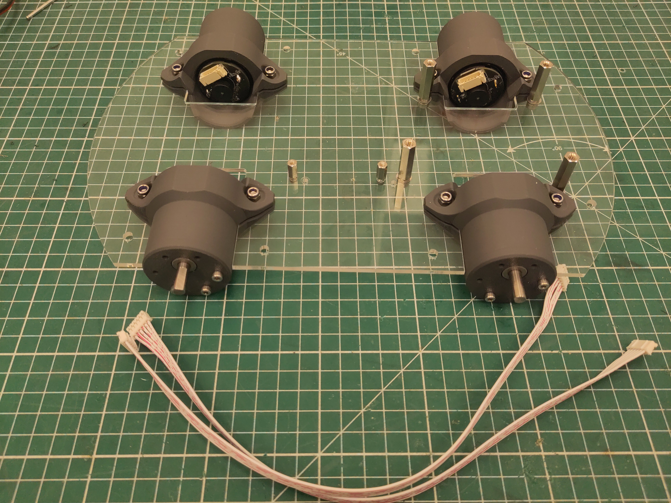
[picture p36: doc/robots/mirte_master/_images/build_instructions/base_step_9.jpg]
   

       ..

       Attach the 30cm JST PH cable to the rear motors.      

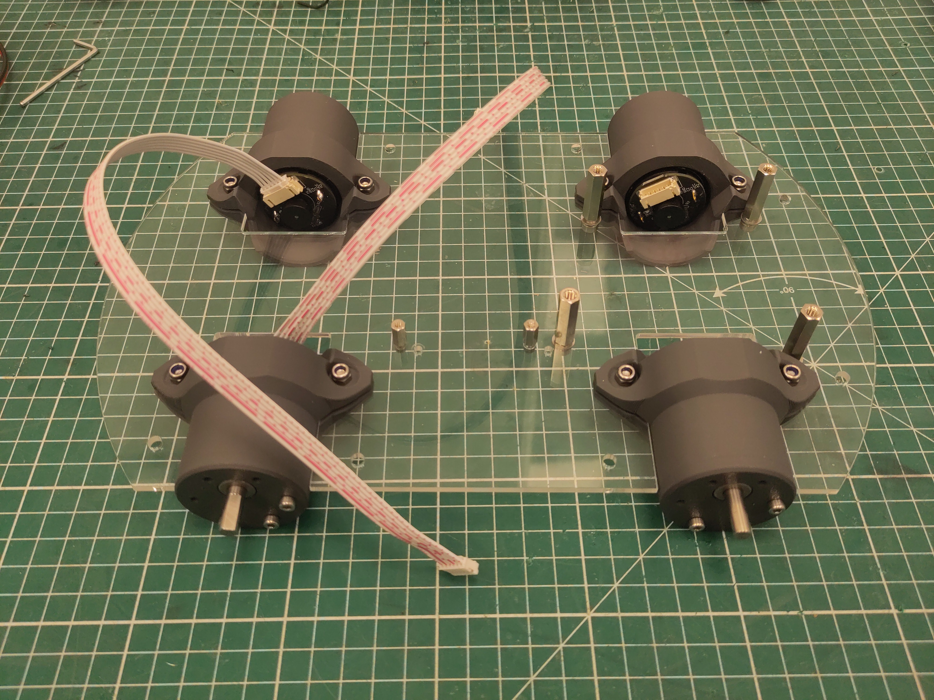
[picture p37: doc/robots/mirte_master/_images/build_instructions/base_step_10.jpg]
   
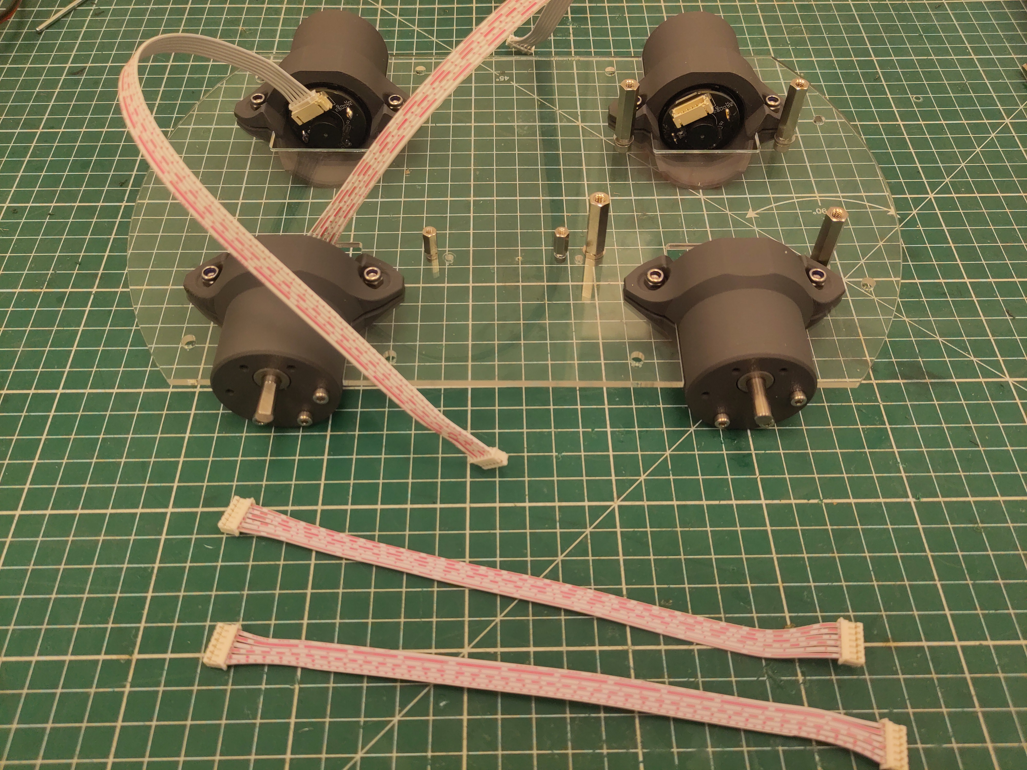
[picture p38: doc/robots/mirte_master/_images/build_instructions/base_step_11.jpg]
   

       ..

       Attach the 20cm JST PH cable to the front motors. 

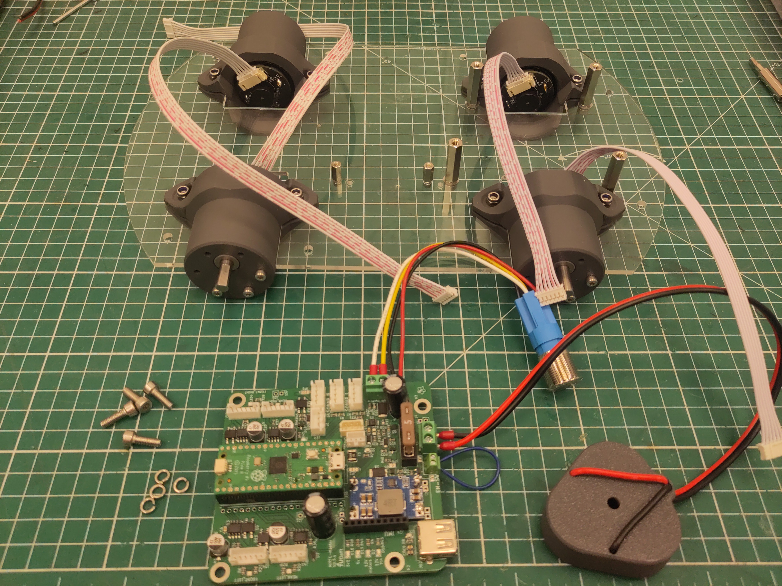
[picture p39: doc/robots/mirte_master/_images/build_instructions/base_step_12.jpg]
   

       ..

       Add the PCB using M4 x 16 screws (with spring washers). 

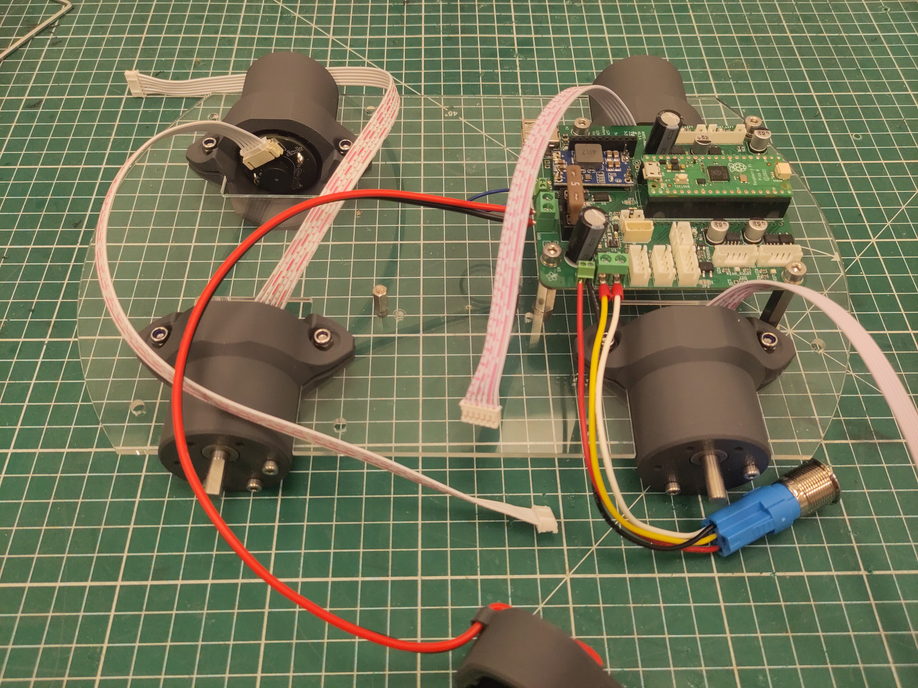
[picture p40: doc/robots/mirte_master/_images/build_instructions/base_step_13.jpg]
   
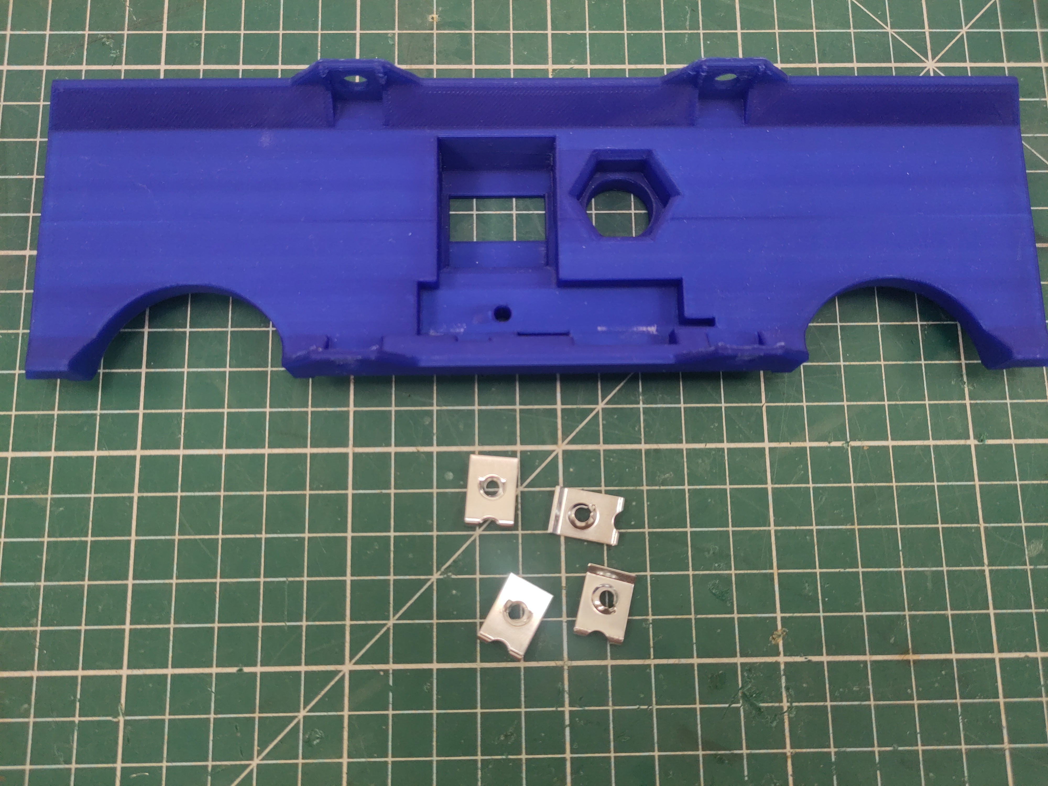
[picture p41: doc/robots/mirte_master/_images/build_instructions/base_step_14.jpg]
   

       ..

       Attach the M4 U-clip captive nut to the side plate. 

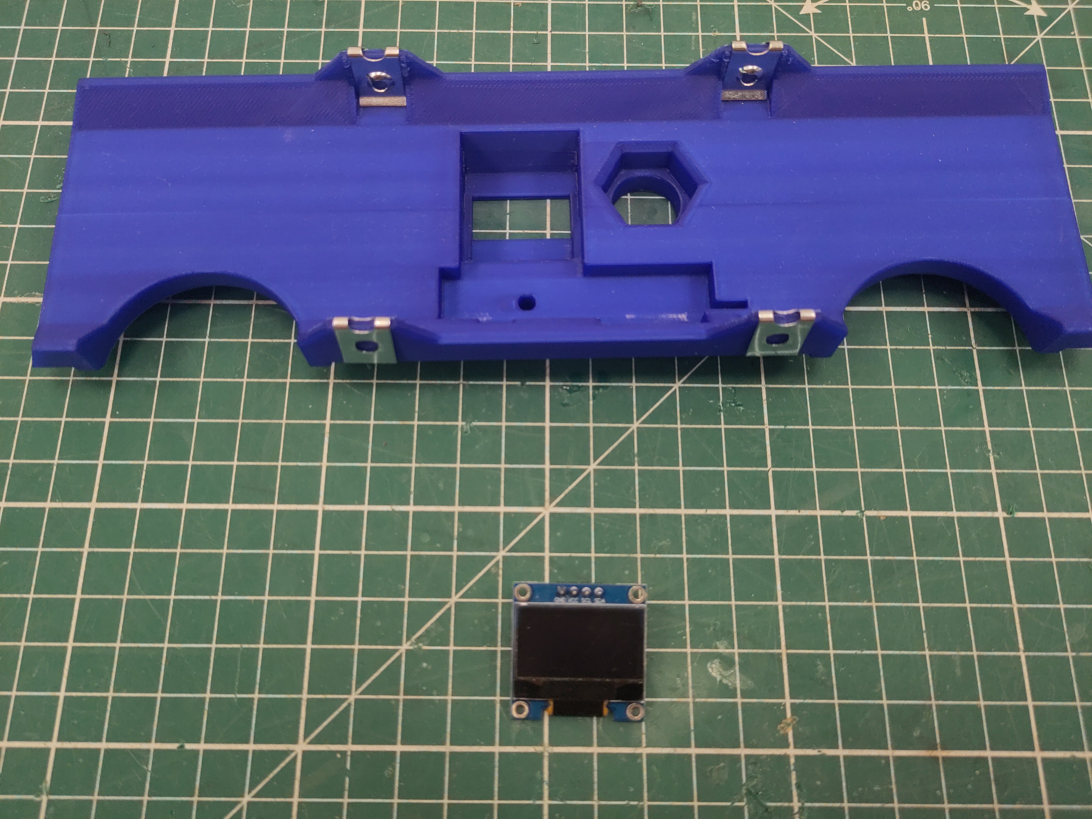
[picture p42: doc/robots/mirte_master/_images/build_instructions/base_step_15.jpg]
   
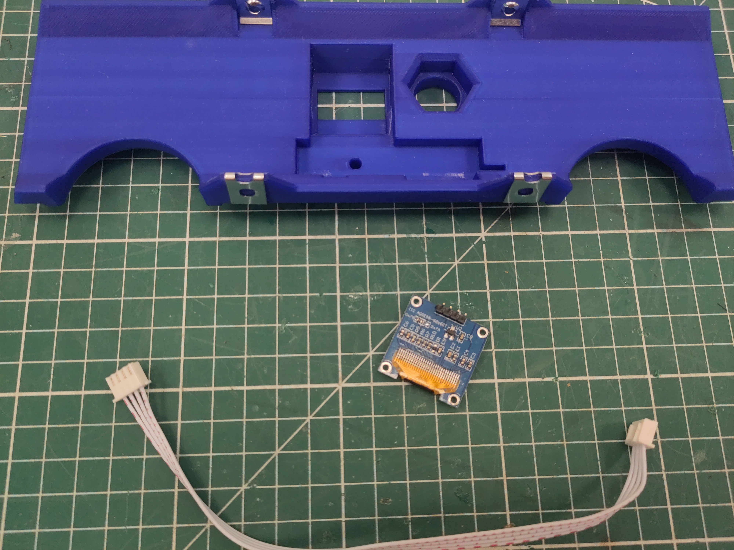
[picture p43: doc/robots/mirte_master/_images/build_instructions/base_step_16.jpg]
   
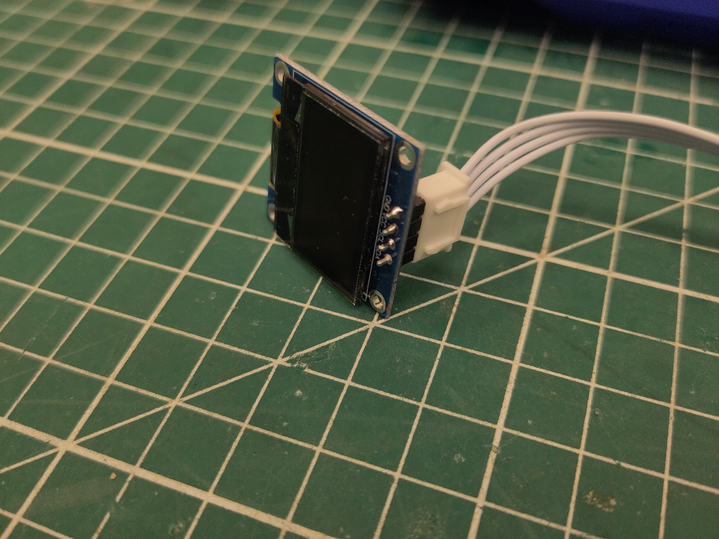
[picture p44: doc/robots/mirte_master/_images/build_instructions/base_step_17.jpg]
   

       ..

       Attach the 20cm JST XH cable to the oled (notice the orientation). 

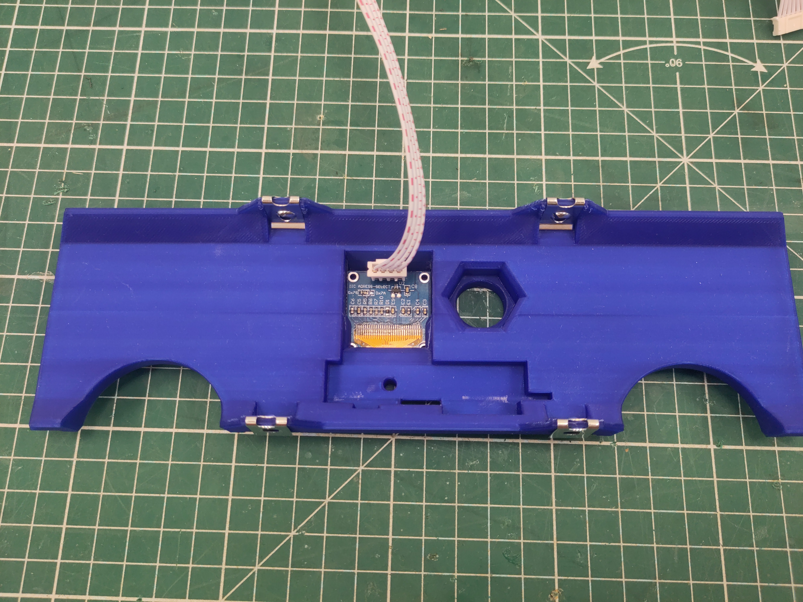
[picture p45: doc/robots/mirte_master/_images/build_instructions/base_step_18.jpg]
   

       ..

       And slide the oled into the side plate. 

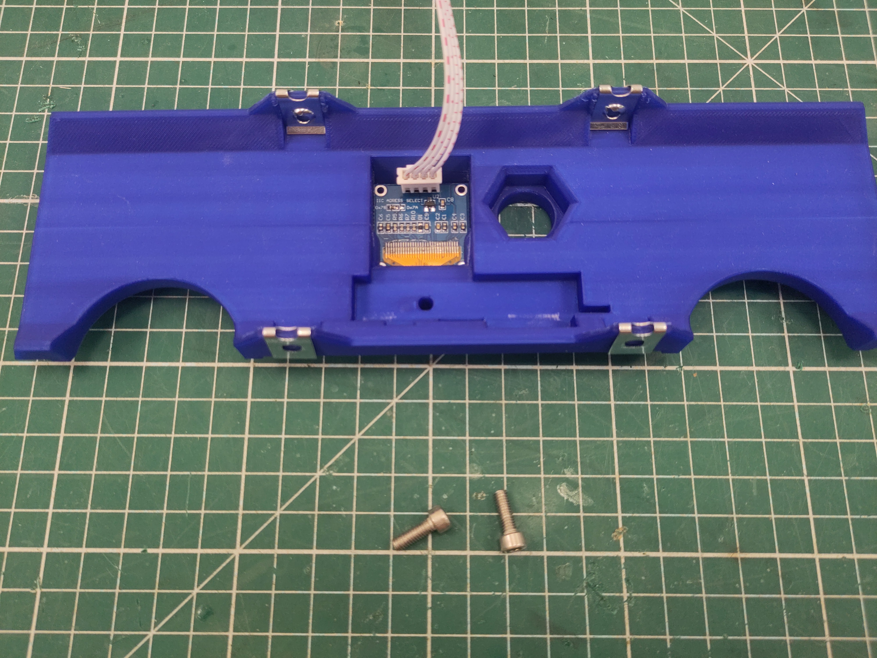
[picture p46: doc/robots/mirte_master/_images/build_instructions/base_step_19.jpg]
   

       ..

       Use M4 x 16 screws to attach the side plate to the bottom plate. 

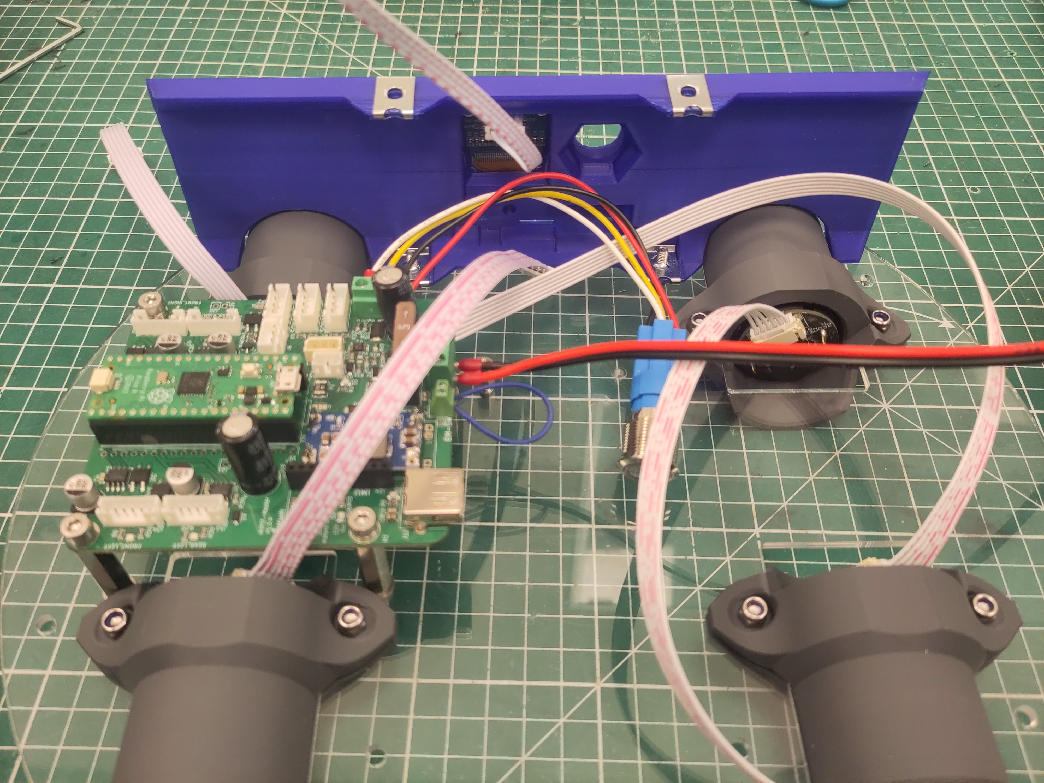
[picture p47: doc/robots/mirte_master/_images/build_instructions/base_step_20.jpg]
   
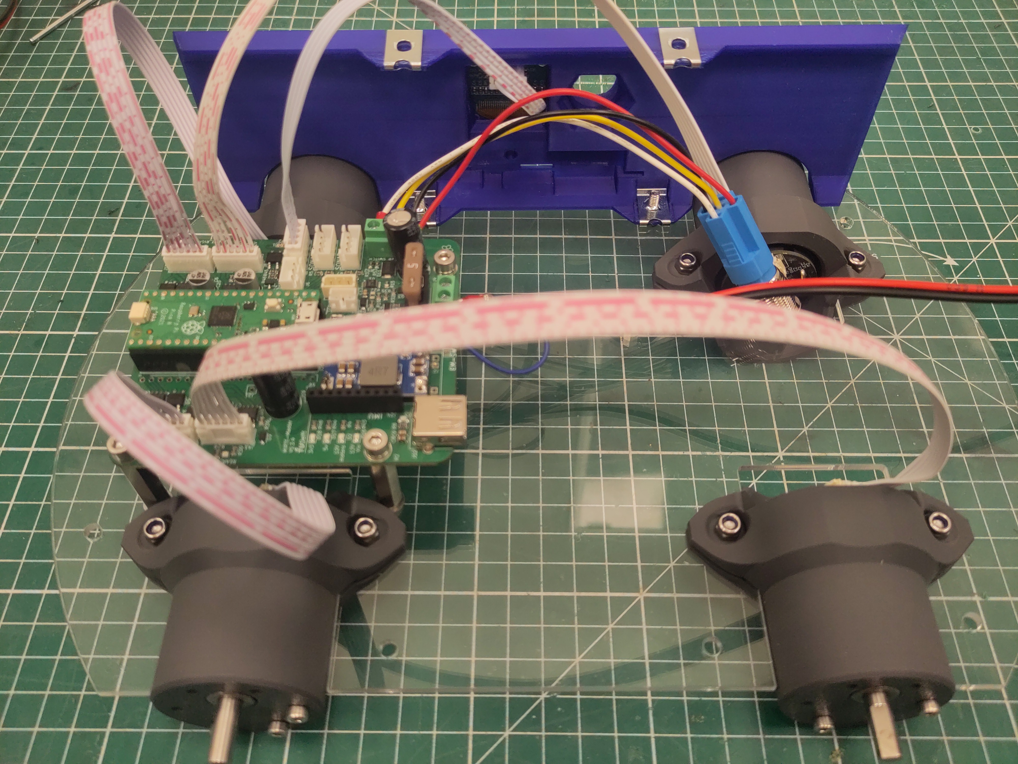
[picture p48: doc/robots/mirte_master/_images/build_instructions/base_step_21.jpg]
   

       ..

       Connect the JST cables of the motors and the oled. 

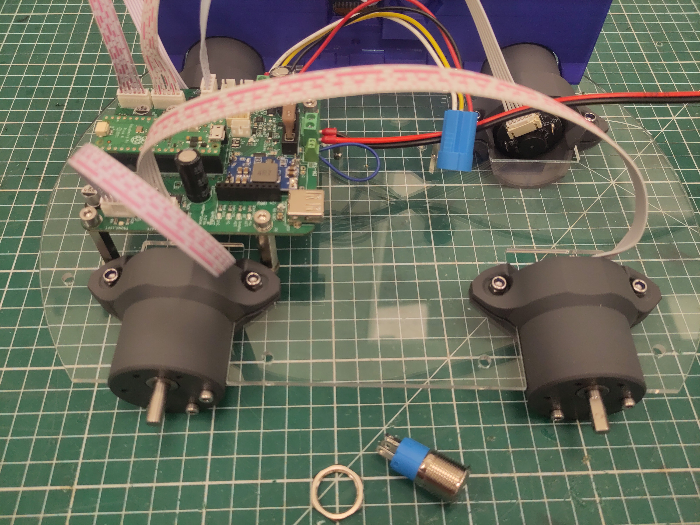
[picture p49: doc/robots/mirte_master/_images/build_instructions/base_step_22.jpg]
   

       ..

       Take the hexagon ring of the switch and attach the button to the
       side panel. 

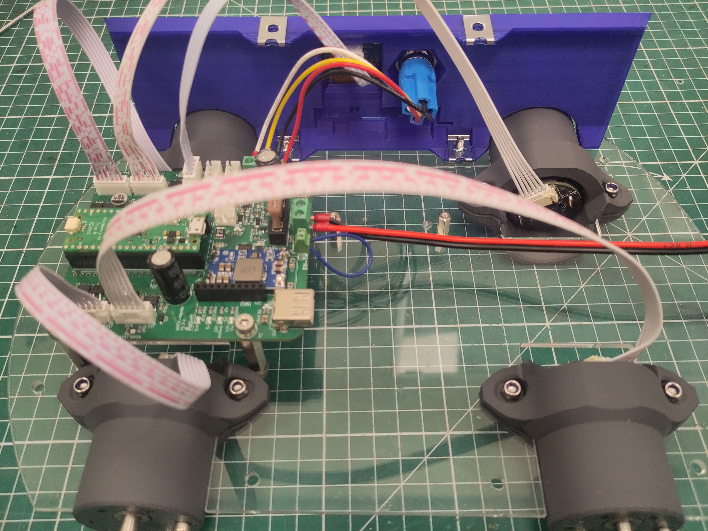
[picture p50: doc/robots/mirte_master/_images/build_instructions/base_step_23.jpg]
   
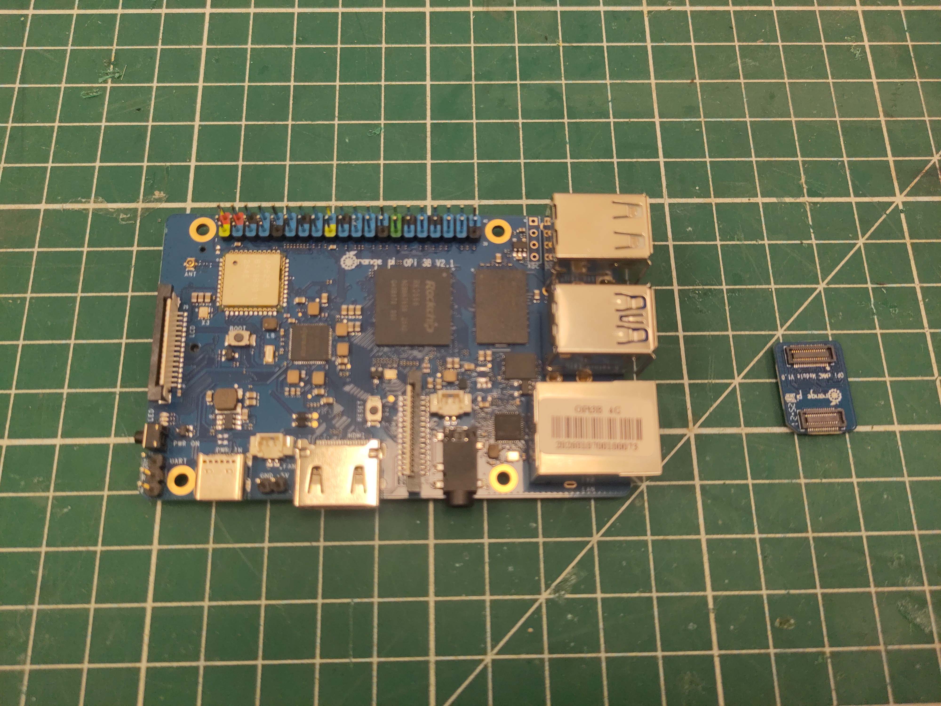
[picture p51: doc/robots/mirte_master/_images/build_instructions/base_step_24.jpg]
   
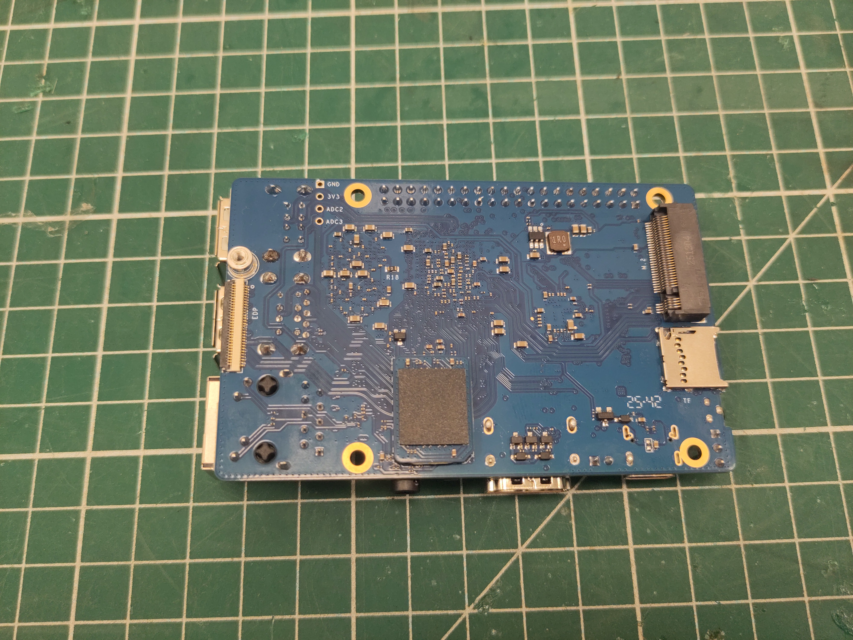
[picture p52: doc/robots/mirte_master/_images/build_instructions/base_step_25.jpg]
   

       ..

       Add the EMMC to the Orange Pi. 

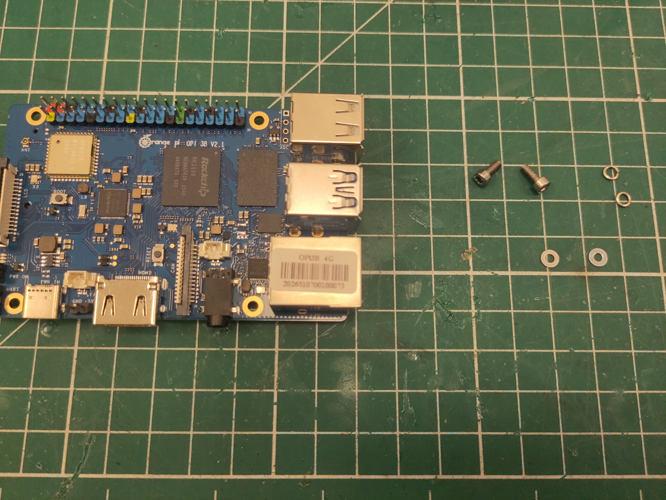
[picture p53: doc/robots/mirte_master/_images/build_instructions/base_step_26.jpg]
   
        
       ..

       Use M2.5 x 6 screws (with washer and spring washer) to place the
       Orange Pi. 

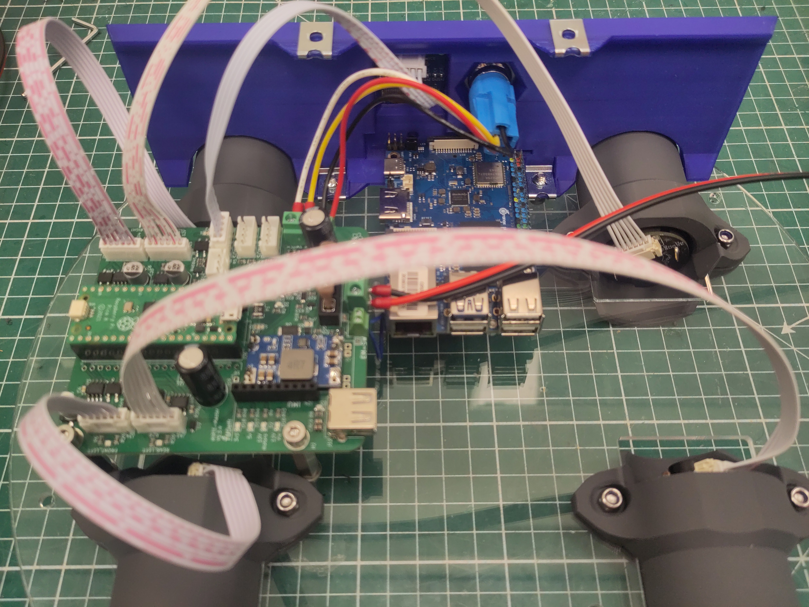
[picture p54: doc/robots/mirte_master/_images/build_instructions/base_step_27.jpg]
   

       ..

       You might need to loosen the M4 screws of the side panel a bit
       to correctly place the Orange Pi. 

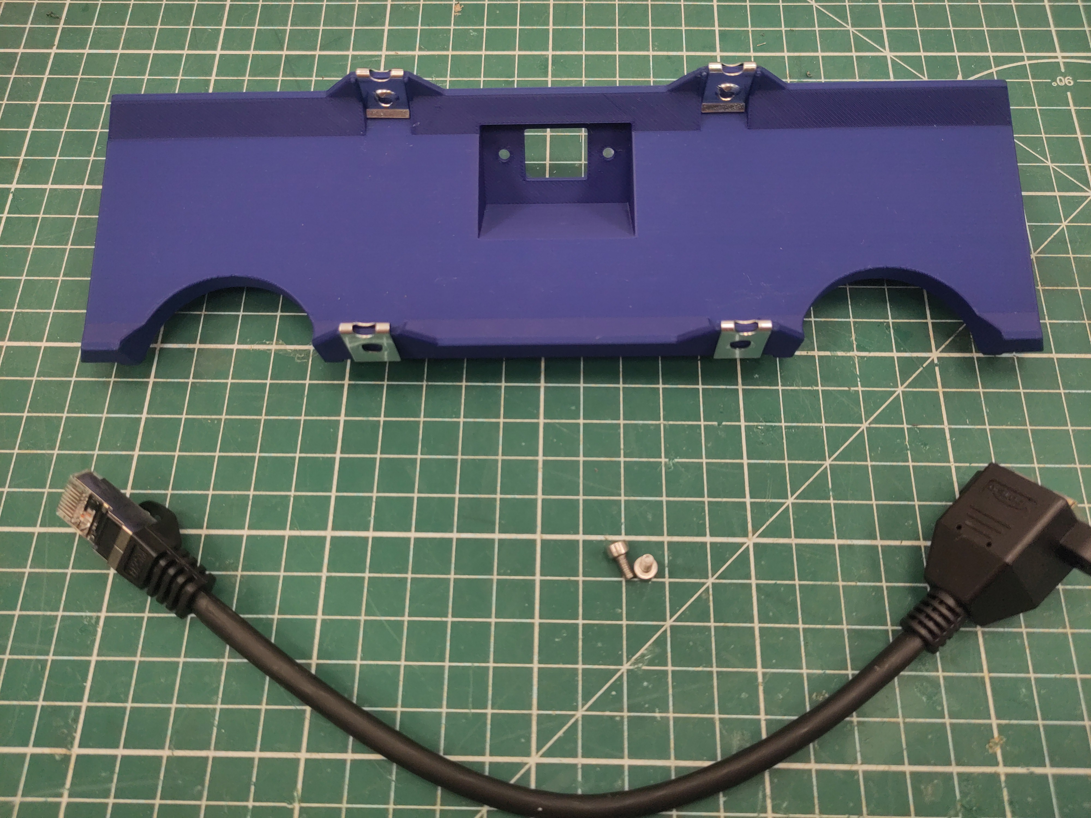
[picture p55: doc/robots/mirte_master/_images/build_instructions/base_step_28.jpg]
   

       ..

       Attach the M4 U-clip captive nut to the side plate. 

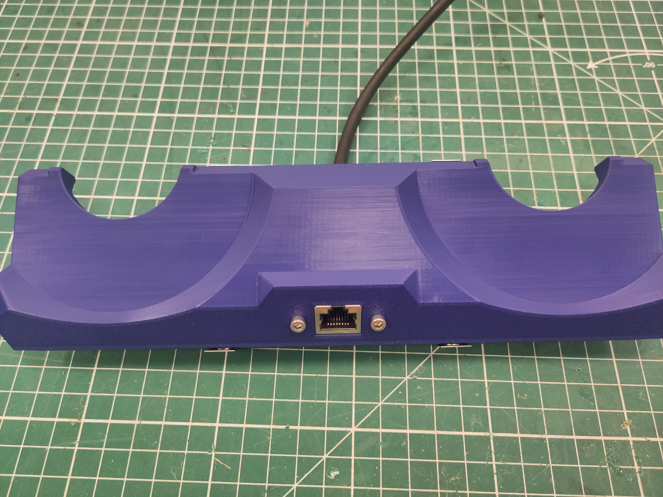
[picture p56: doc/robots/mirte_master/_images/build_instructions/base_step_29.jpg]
   

       ..

       Attach the ethernet extension cable using M3 x 6 screws. 

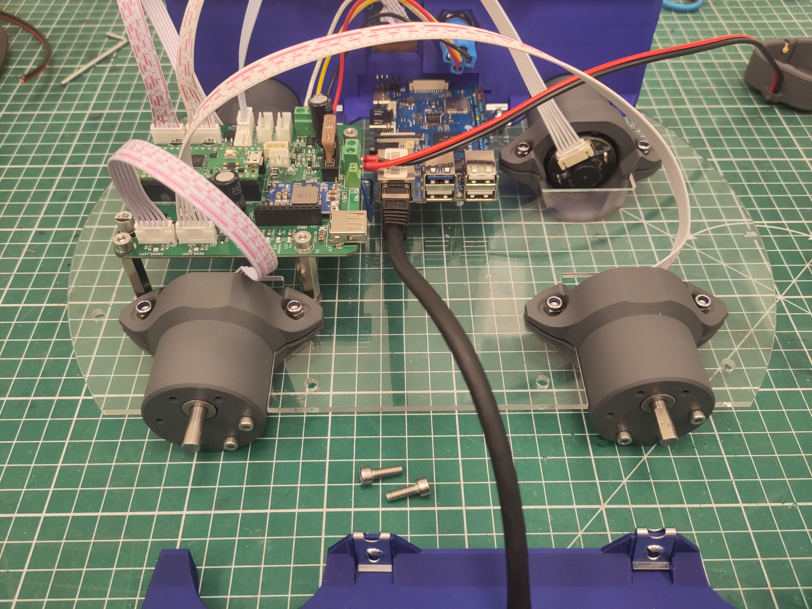
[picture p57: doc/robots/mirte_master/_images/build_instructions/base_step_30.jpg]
   

       ..

       Use M4 x 16 screws to attach the side plate to the bottom plate.  

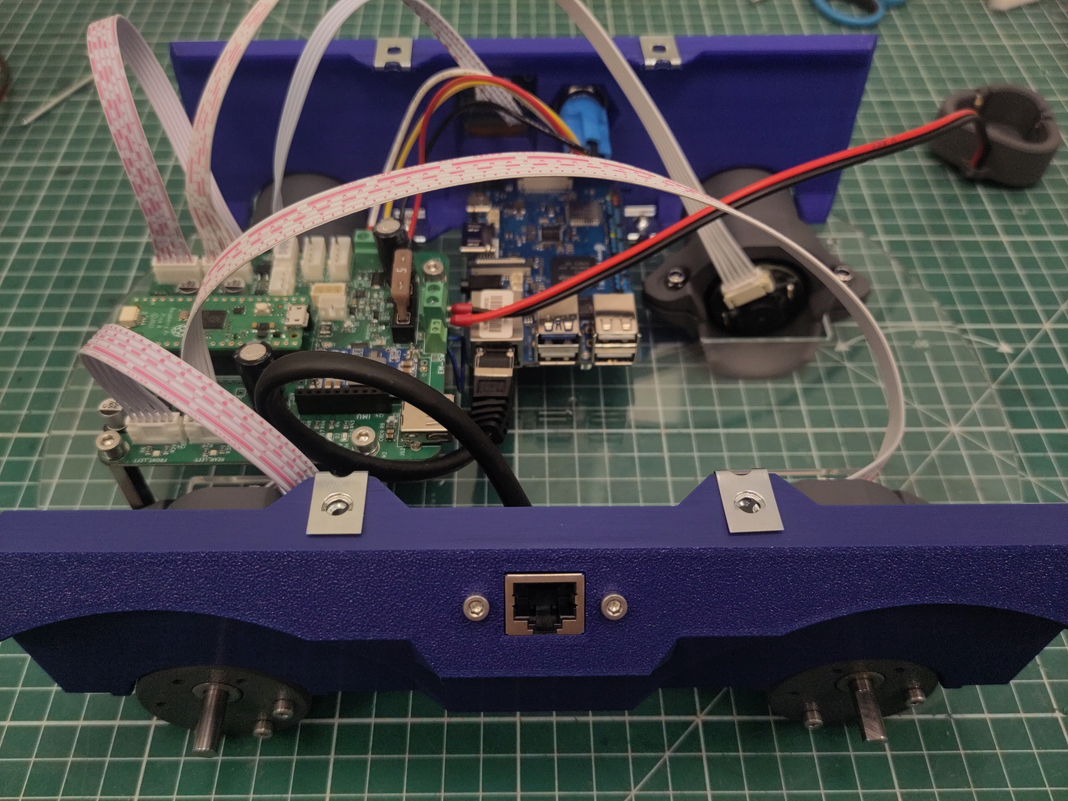
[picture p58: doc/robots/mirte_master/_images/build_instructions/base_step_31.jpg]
   
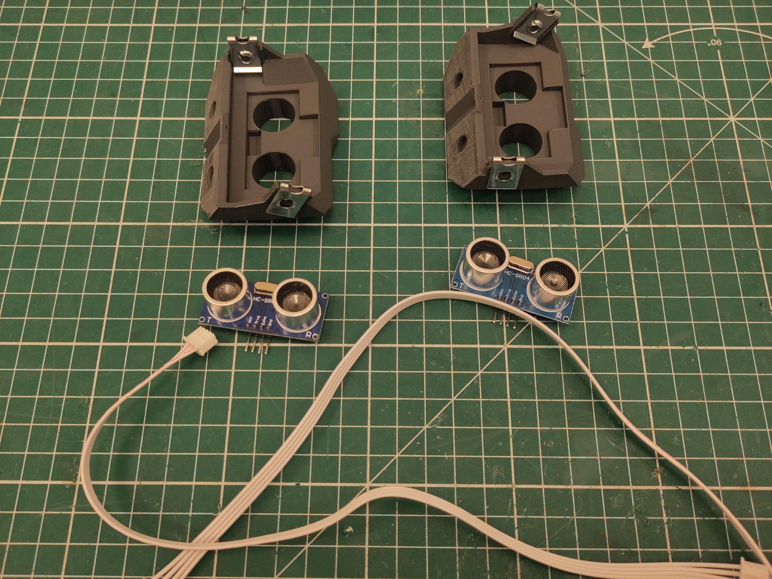
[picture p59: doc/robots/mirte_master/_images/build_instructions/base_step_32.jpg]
   

       ..

       Attach the M4 U-clip captive nut to the ultrasonic modules.  

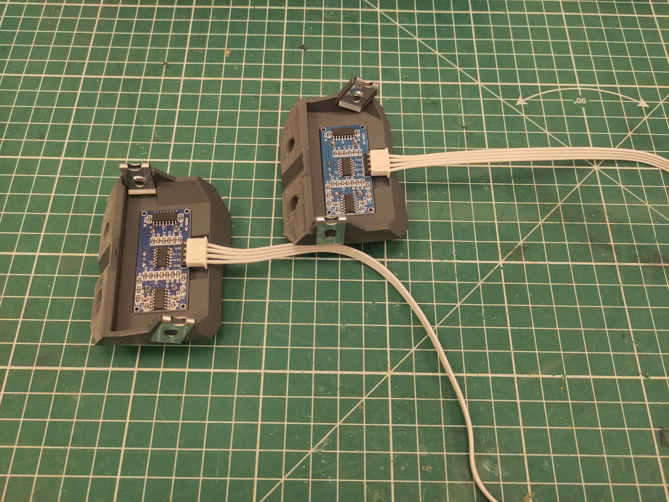
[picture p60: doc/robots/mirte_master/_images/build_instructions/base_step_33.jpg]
   

       ..

       Connect the 30cm JST cables to the sensors (notice the orientation), and
       place them in the modules.  

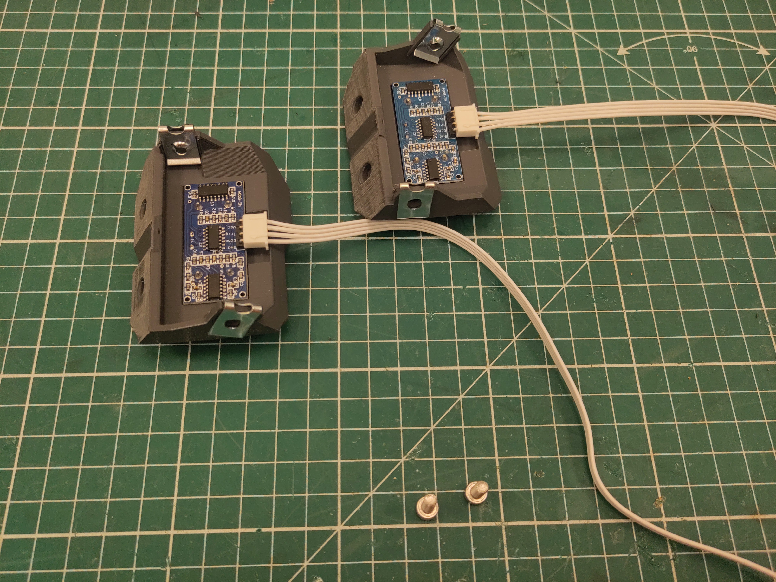
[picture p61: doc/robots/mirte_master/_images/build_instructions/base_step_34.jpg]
   
        
       ..

       Use M4 x 16 screws to attach the modules to the base plate.  

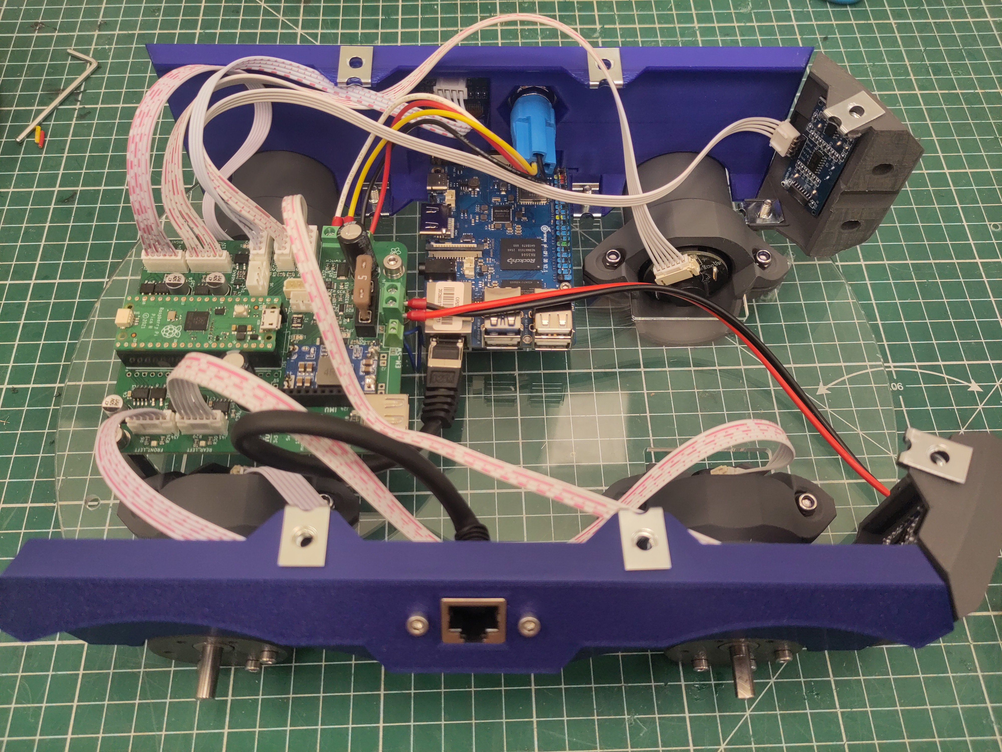
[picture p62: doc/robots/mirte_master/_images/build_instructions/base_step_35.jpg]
   

       ..

       Dismount the screws on the bottom of the battery.  

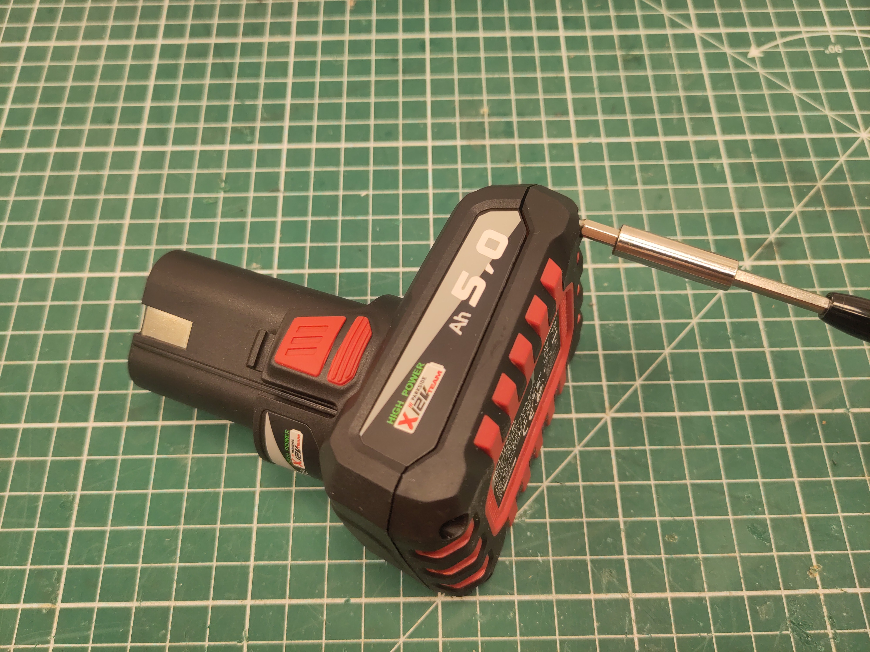
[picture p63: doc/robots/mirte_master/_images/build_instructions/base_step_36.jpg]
   
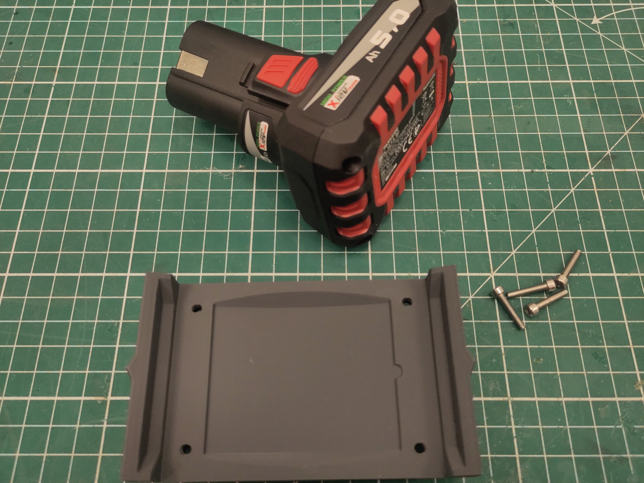
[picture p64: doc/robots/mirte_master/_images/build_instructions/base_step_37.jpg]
   
        
       ..

       Use M3 x 16 screws to attach the battery module to the battery.  

   
   

       ..

       Attach the M4 U-clip captive nut to the ultrasonic modules.  

   

       ..

       Use 3 of the M2.5 x 6 screws to attacht the lidar.  

   
        
       ..

       Use the last M2.5 x 6 screws to attacht uart-board to the lidar.

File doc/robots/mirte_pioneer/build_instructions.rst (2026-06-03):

Build instructions
##################

The MIRTE Pioneer uses a wooden frame. You can use the build instructions
steps below to build your robot.

.. tabs::

   .. group-tab:: MIRTE PCB

      .. carousel::
         :show_controls:
         :show_buttons_on_top:

         
         
         
         
         
         
         
         
         
         
         
         
         
         
         
         
         
         
         
         
         
         
         
         
         
         
         
         
         
         
         
         
         
         
         
         
         
         
         
         
         
         
         
         
         
         
         
         

   .. group-tab:: Breadboard (Pico as example)

      .. carousel::
         :show_controls:
         :show_fade:
         :show_dark:
         :show_buttons_on_top:

         
         
         
         
         
         
         
         
         
         
         
         
         
         
         
         
         
         
         
         
         
         
         
         
         
         
         
         
         
         
         
         
         
         
         
         
         
         
         
         
         
         
         
         


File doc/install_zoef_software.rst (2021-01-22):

Install Zoef Software
#####################

For Zoef to work we need to install software on both the SD card as on the microcontroller. This part only covers the installation of the SD software.

Download prebuilt SD card image
===============================
.. warning::
   The prebuilt SD card will currentl only work on the Orange Pi Zero. All other plaforms will have to install from source (which will be supported later).

1. Download the SD card image from here.
2. Burn the image onto the SD card with for example Balena Etcher.
3. Put the SD card in the Orange Pi Zero.

Install from source (Not supported Yet)
=======================================
.. warning::
  Installing from source might fail on the Orange Pi Zero due to low specs. Installing from source is only recommended when using a more powerful computer.

.. prompt:: bash $

    wget https://github.com/zoef_robot/zoef_install_scripts/raw/install_zoef.sh | sh

Please get yourself a cup of coffee, this might take some time........

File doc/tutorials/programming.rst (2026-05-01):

Programming MIRTE
#################

The goal of MIRTE is to get everyone to learn about robotics. This means that there are multiple layers of complexity available.

Blockly
=======

The easiest way to program your MIRTE robot is to use Blockly. Depending on your settings,
you should be able to drag and drop different blocks onto the canvas. By doing so, you
can create your own logic for the robot.

      Blockly programming

Running this code can be done in the control bar on the top. It is also possible to pause your
code from running (not that sensor values of course keep changing), step through your code, and
stop your program from running.

      MIRTE control bar

.. note::
   When your program is finished running the robot will automatically also stop the motors
   from running. This is to make sure that you do not forget to stop the motors. This also
   means that only including a setMotorSpeed will not make your robot move.

Python
======

One level more advanced is programming your MIRTE robot in Python. This can be done in two ways.

From web interface
------------------

Below the Blockly canvas you can also find the Python code generated by Blockly. You can just
modify the Python-code and run it with the same control bar as Blockly.

      Blockly Python from Web interface

In Jupyter Notebook
-------------------

Jupyter is disabled by default (due to high RAM usage on the Orange Pi Zero 2). You can start it as a service:

.. code-block:: bash

   mirte$ sudo systemctl start mirte-jupyter

Jupyter will run on http://mirte.local:8888 (note: it might take some time for Jupyter to start) showing some 
examples from Jupyter-ROS (which are located at /home/mirte/jupyter-ros). If you want Jupyter to start on boot you can run:

.. code-block:: bash

   mirte$ sudo systemctl enable mirte-jupyter

You can now enter Jupyter by brwosing to http://mirte.local:8888 and start a new notebook:

Python programming from Jupyter

From terminal
-------------

Of course it is also possible to progrma the robot from withun the Python interpreter,
or your own Pytohn script. 

.. code-block:: python

   >>> from mirte_robot import robot
   >>> mirte = robot.createRobot()

Using onboard VS-code
---------------------

The MIRTE robot has VS-code installed, which can be accessed though http://mirte.local/code.

ROS
===

In Jupyter Notebook
-------------------

Jupyter is disabled by default (due to high RAM usage on the Orange Pi Zero 2). You can start it as a service:

.. code-block:: bash

   mirte$ sudo systemctl start mirte-jupyter

Jupyter will run on http://mirte.local:8888 showing some examples from Jupyter-ROS (which are located at /home/mirte/jupyter-ros). If you want Jupyter to start on boot you can run:

.. code-block:: bash

   mirte$ sudo systemctl enable mirte-jupyter

From terminal
-------------

When MIRTE boots a systemd service will launch the MIRTE bringup. This service can be stopped and started manually as well:

.. code-block:: bash

   mirte$ sudo systemctl stop mirte-ros
   mirte$ sudo systemctl start mirte-ros

You can also run the launchfile yourself (only when you stopped the systemd service):

.. tabs::

   .. group-tab:: MIRTE Pioneer

      .. code-block:: bash

         mirte$ ros2 launch mirte_bringup minimal.launch.py

   .. group-tab:: MIRTE Master

      .. code-block:: bash

         mirte$ ros2 launch mirte_bringup minimal_master.launch.py

Using onboard VS-code
---------------------

The MIRTE robot has VS-code installed, which can be accessed though http://mirte.local/code.

Using ROS icw Python API
------------------------

Although not preferred, at some point it might be useful to combine the existing Python API
with ROS. This can be done, but in that case you do not need to start a ROS node anymore.
The example below will listen to a `Twist <http://docs.ros.org/en/noetic/api/geometry_msgs/html/msg/Twist.html>`_ 
message published on cmd_vel and then use the Python API to drive around.

.. code-block:: python

   # Import and load the mirte API
   from mirte_robot import robot
   mirte = robot.createRobot()

   # Import rospy
   import rclpy
   from rclpy.node import Node
   from geometry_msgs.msg import Twist

   class MinimalSubscriber(Node):

     def __init__(self):
       super().__init__('dummy_control')
       self.create_subscription(Twist, "/mirte_base_controller/cmd_vel", callback, 10)
       self.subscription

     # Move the robot based on the twist message
     def callback(self, twist_msg):
       speed = 0
       if (twist_msg.linear.x > 0.0):
         speed = 80

       mirte.setMotorSpeed('left', speed)
       mirte.setMotorSpeed('right', speed)

   def main(args=None):
     rclpy.init(args=args)

     minimal_subscriber = MinimalSubscriber()
     rclpy.spin(minimal_subscriber)
     minimal_subscriber.destroy()
     rclpy.shutdown()

   if __name__ == '__main__':
      main()

Creating your own ROS packages/nodes
------------------------------------

MIRTE already uses a ROS workspace located at ~/mirte_ws. The easiest way to get started
is to use this workspace an create your own packages and nodes in this workspace. You can 
achieve this by executing the following commands:

.. code-block:: bash

   mirte$ cd ~/mirte_ws/src

And follow the `instructions to create new packages <https://docs.ros.org/en/humble/Tutorials/Beginner-Client-Libraries/Creating-Your-First-ROS2-Package.html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>`_.

And of course one had to fill ~/mirte_ws/src/my_own_package/scripts/my_node.py with the
logic you want to be executed.

If you would also like to have this node to be started at boot you can add this to the 
launchfile in ~/mirte_ws/scr/mirte_packages/mirte_bringup/minimal.launch. That is the 
file that will be executed as you can see in /usr/local/src/mirte/mirte-install-scripts/services/mirte-ros.service.

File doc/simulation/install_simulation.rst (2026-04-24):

Installation
############

.. note:: 

   We currently only have a Gazebo Classic simulation of the MIRTE robots.

The simulation will not run on the MIRTE robot, but on your own machine.
We assume you have ros-humble-base installed. To get the simulation up and
running you need to install a couple of packages in your ROS2 workspace
(eg ~/ros2_ws/):

.. code-block:: bash

   $ git clone https://github.com/mirte-robot/mirte-gazebo src/mirte-gazebo
   $ vcs import src/ < mirte-gazebo/sources.repos

Optionally, you can remove the unused ROS packages. This will make the 
install, and build go much faster. Only do this as long as you have no 
changes in these folders.

.. code-block:: bash

   $ cd src/mirte-ros-packages
   $ rm -r mirte_bringup/ mirte_telemetrix_cpp/ mirte_teleop/ mirte_test/ mirte_zenoh_setup/
   $ cd ../..

And finally install the dependencies and build everyting:

.. code-block:: bash

   $ rosdep install --from-paths src --ignore-src -r -y
   $ colcon build --symlink-install
   $ source install/setup.bash

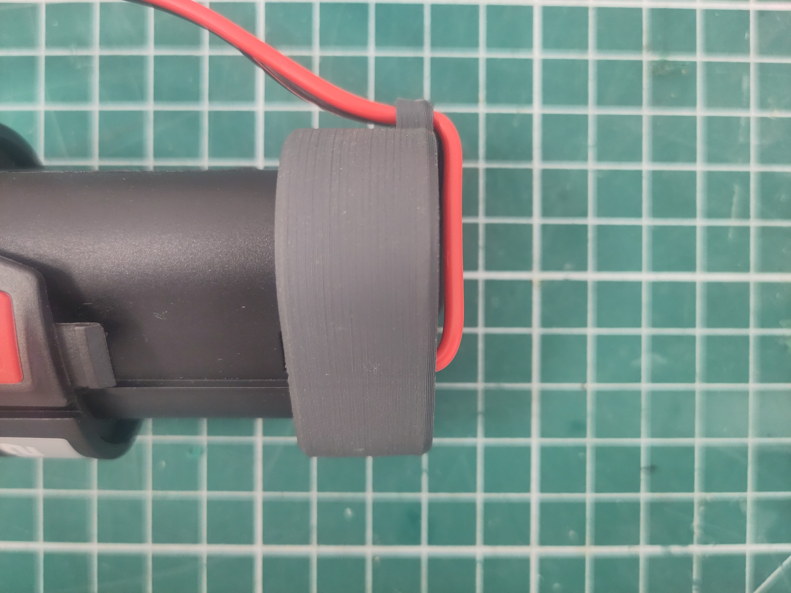
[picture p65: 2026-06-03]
doc/robots/mirte_master/_images/build_instructions/servo_step_2.jpg

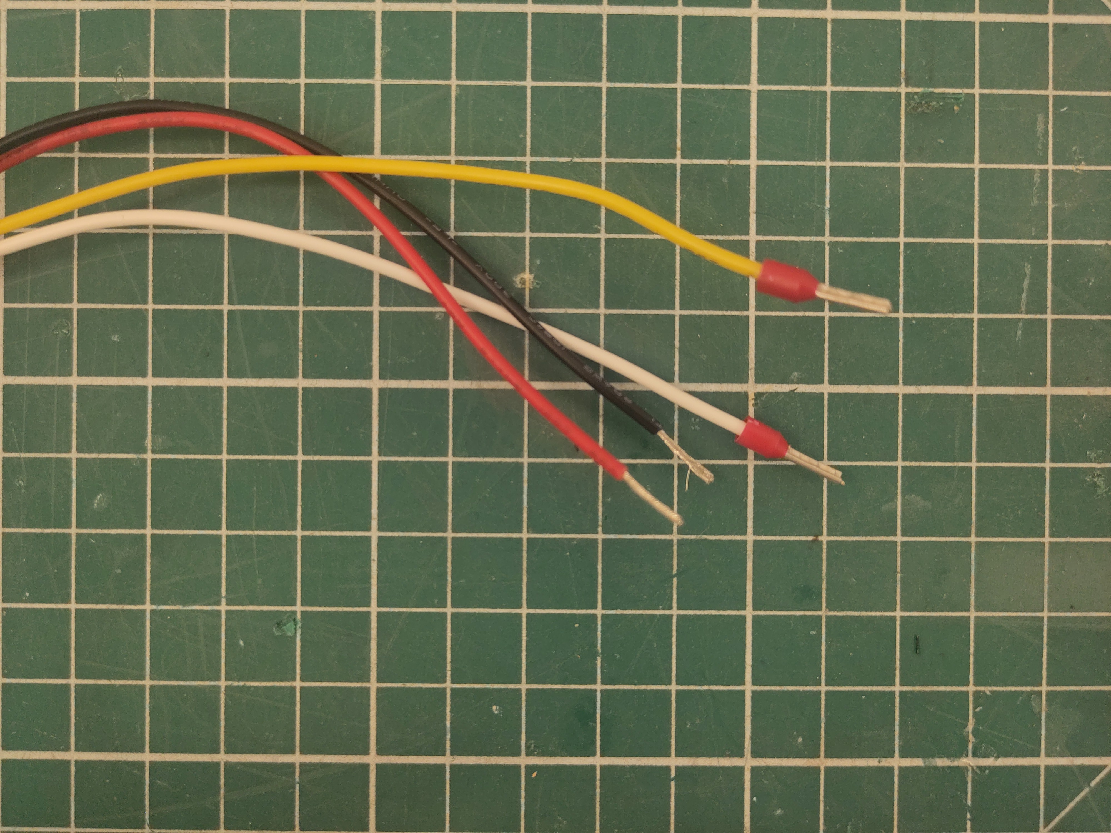
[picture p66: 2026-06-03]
doc/robots/mirte_master/_images/build_instructions/pcb_step_18.jpg

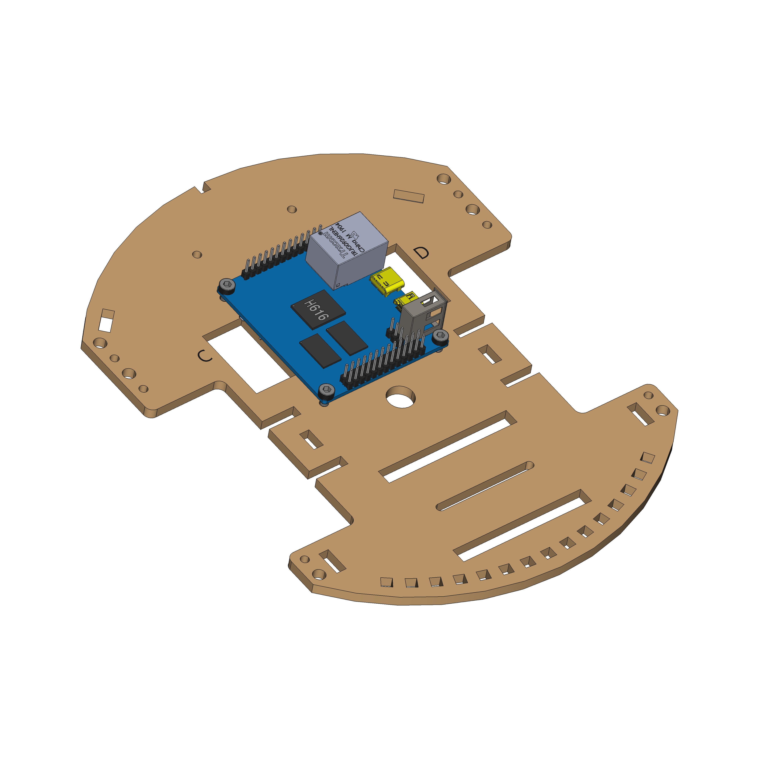
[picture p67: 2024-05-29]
doc/_images/build_instructions/breadboard/1_step3.png

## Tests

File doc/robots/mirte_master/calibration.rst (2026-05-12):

Calibration
###########

Now that we have assembled the robot we might need to tune some of the settings
for the robot to operate correctly.

Base PID
--------

Change PID parameters of the base controller with:

``$ ros2 param set /pid_wheels_controller gains.front_left_wheel_joint.p 1.0``

``$ ros2 param set /pid_wheels_controller gains.front_left_wheel_joint.i 1.0``

``$ ros2 param set /pid_wheels_controller gains.front_left_wheel_joint.d 1.0``

Arm position
------------

Although you tried the best you could to assemble the arm in the home (i.e.
upright) position, it is impossible to have this exactly right. We therefore
still need to calibrate the servo's

``$ ros2 run mirte_test mirte_master_calibrate.py``

.. warning::

   This script should unlock the servo's. If you feel that one of the servo'saw
   is still locked (i.e. you are unable to change it), please restart the script.
   Due to a bug, the Elbow (HTD-35H) might stay locked.

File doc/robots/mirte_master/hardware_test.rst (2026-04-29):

Hardware tests
##############

Before we can actually test the robot, we need to install the software. 
You can follow the instructions from here and either install the MIRTE-OS
on the EMMC, or run it from SD card.

Please note that at the moment you will need to get some development image
located at: https://github.com/ArendJan/mirte-sd-image-tools/actions/runs/24549626442

This also holds for the uf2 for the Pico. Please upload this one:
https://github.com/ArendJan/Telemetrix4RpiPico/releases/tag/rolling

Please note that currently these images are using the development MIRTE ROS 
packages from: https://github.com/ArendJan/mirte-ros-packages/tree/develop

After booting you can login to the robot, and run the following test:

``$ ros2 run mirte_test mirte_master_hw_test``

Please note that you need to make sure the distance sensor gets some data (e.g.
moving your hand in front of the sensor)

.. warning::

   Sometimes the timing of some of the sensordata (e.g. lidar and/or camera) is 
   off which currently will fail the test. In that case you can check if you
   get data on the missing topics.

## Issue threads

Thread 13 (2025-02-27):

Motor connection instructions not consistent

knmcguire, 2025-02-27:
The motor connection instructions are inconsistent.

The PDF shows the right way, but because it's upside down it required some thinking.

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

But the breadboard instructions are showing it the other way around:

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

So I installed the motors the other way around. Perhaps it went wrong with that the image was flipped but not the cables?

Also it helps to give the motors on the website instructions some names.

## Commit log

2021-10-21 Added fritzing diagrams to the documentation
    [full_PCB.fzz, full_nano.fzz, full_uno.fzz]
2024-03-25 add images + assembly instructions
2024-03-25 Fix link compute pcb
2024-05-01 fix link powerbank
2024-05-07 Update mirte master arm positions
2024-05-07 bus servo terminal
2024-05-08 Add servo id instructions
2024-05-27 upd pid base mirte-master
2024-10-16 improve hardware list, bolts length and micro sd
2024-11-18 start mirte master BOM
2024-11-21 Fix double charger item part list
2024-11-21 add battery link
2024-12-16 Update mirte master electro assembly
2025-02-11 Start actuators v2 docs
2025-02-11 add current tag ci
2025-02-11 print depth
2025-02-11 remove some prints
2025-04-11 Redid MIRTE Master BOM
2025-04-11 Renamed current to develop, and default to a specifi version instead of develop
2025-05-07 Add note pwm driver i2c address
2025-07-17 Added ned PCB to cable instructions
2025-07-17 Added new PCB and build instructions
2026-04-24 fix failing build if it is current release
2026-04-29 Added initial MM BOM
2026-05-12 Updated PID setting param
2026-06-01 Added mounting elements to MM bom
2026-06-01 Renamed hardware specs to bom
